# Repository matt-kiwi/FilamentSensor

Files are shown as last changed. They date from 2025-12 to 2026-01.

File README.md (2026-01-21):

# Filament sensor and controller

## Project summary / purpose

Used in the manufacturing process of making and recycling plastic. Specifically to detect if a strand of filament has been broken, then alert the operator with an audio alarm.

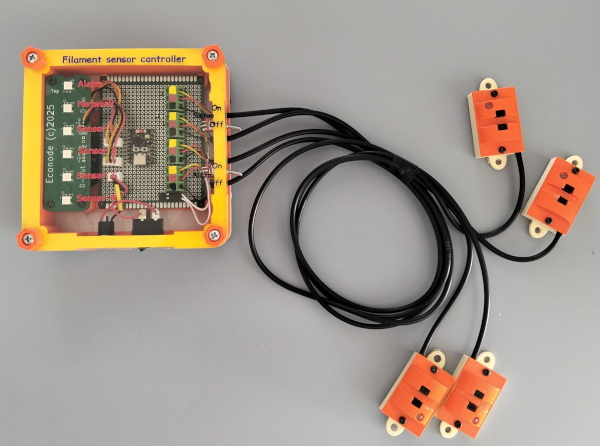
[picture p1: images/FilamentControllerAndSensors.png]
Filament Controller and Sensors


### Dedicated to Bill and Eva

This device is dedicated to Bill and Eva of KiwiFil plastics in New Zealand. And their pioneering work with plastics recycling.

## Usage and wiring

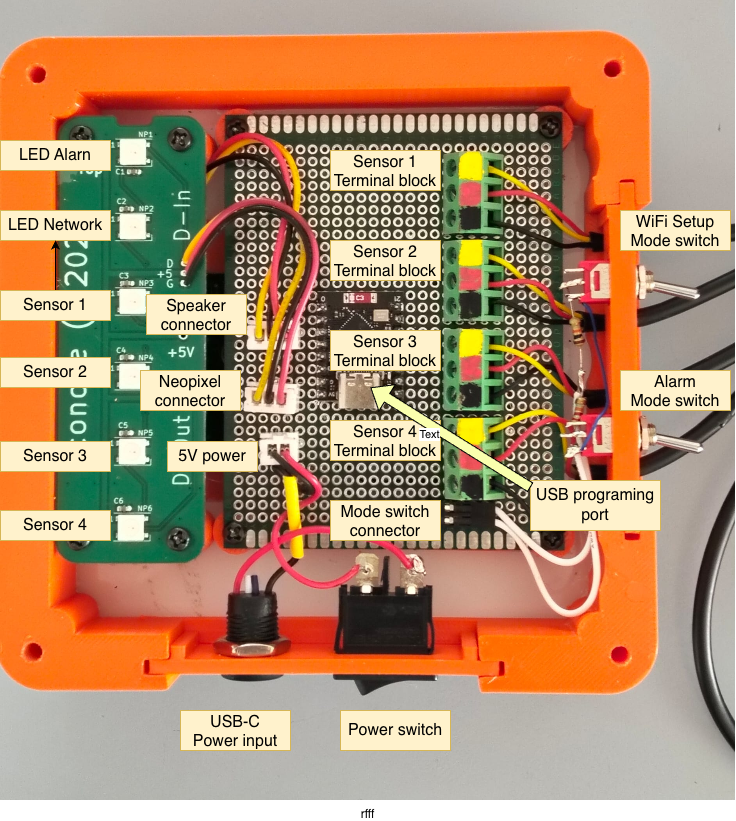
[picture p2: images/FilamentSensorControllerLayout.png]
Filamanet controller with labels


### Wiring

- Remove top lid with finger screws.
- Pull out switch block assembly / cable entry plate.
- Connect all 4 filament sensors using screw terminals, if a sensor is missing bridge Ground and Sensor input (Yellow).
- Install switch block assembly aligning sensor cables in combe/clamp.
- Install top lid

***Note that Siren / 12v Panel use lower 3pin JST for 12v in and Siren out Not shown in picture***

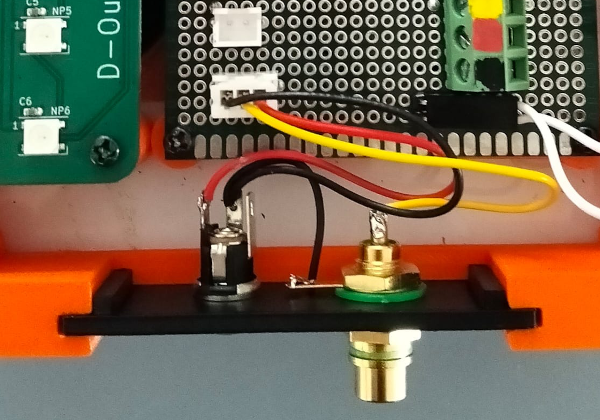
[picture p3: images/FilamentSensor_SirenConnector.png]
Siren panel


### Usage

Controller is powered by USB/5v some USB-C PD power supplies may not work.<br/>
Turn on power switch, during boot up the first LED will be blue, and a power up tune will be played.

\*\* One day when the WiFi software has been written the WiFi setup switch will enable configuring the WiFi

The "Alarm mode" switch enables or disables the audible alarm.

The alarm will sound when any of the sensors fail to detect filament.<br >
LEDs

- Alarm: Red in alarm, Green no alarm
- If a 12v Siren is connected it will sound.
- Sensors 1 - 4: Red in alarm, Green no alarm

Adjusting the volume, the underside of the controller has a 2 Watt speaker and volume control, turn clockwise to increase the volume.
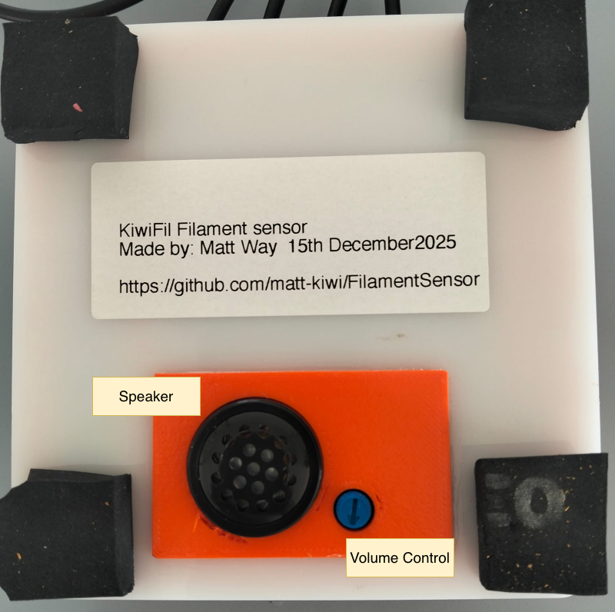
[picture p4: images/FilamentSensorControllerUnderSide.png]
Speaker and volume


## External Alarm / Siren

It was found the small 2w speaker was not loud enough for the factory background noise. So it was decided to attach a external 12volt Siren.

A 12v to 5v power module was added, and a small photo mosfet relay, so the ESP32 can switch on / off a small 12v load.
The optional siren is external and connected by a RCA/Coax connector.

### Siren 105dB

Siren from SurplusTronics  [Siren Piezo 105 dB 12 Volt DC](https://surplustronics.co.nz/products/4066-siren-piezo-105-db-12-volt-dc)

#### Two sirens with RCA plugs

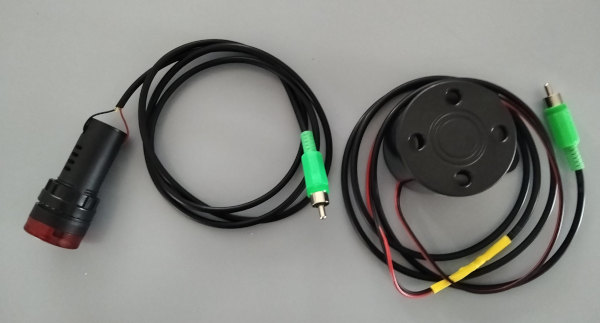
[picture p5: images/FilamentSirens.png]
Sirens on leads


#### 12V DC / Siren panel

Siren panel

## Serial Menu system

Some settings are user settable via the serial menu system, you will need to connect a USB-C cable to the internal USB-C port on the Super Mini, then use your favorite terminal program.

Mine is Cool Term by Roger Meiers [https://freeware.the-meiers.org/](https://freeware.the-meiers.org/)

Press enter twice to see menu options.

```TEXT
Reconnecting to /dev/cu.usbmodem1201 ...         Connected!
[I][MAIN] Initializing system...
[I][MAIN] =================================
[I][MAIN] Filament Sensor by Econode
[I][MAIN] =================================
[I][MAIN] Chip Model: ESP32-C3
[I][MAIN] Chip Revision: 4
[I][MAIN] CPU Frequency: 160 MHz
[I][MAIN] Flash Size: 4 MB
[I][MAIN] Free Heap: 261332 bytes
[I][MAIN] NeoPixel Pin: GPIO2
[I][MAIN] System initialized successfully!
[I][MAIN] =================================

                *############*.                                        
             +##################*-                                     
           .######################*:                                   
          .#########################+                                  
          *###########################=                                
          ##################################*                          
          -##############################% ##*.                        
           ###################################=                        
            +###################################+                      
              ########################+#####-=#####-                   
                .##################               ###=                 
                   ##*:=****=::                     .#*.               
                  ##=                                 .*=              
                 ##*                                    *+             
                ###*                                     :=            
              :#####*                                    =*=           
             *##########+                               -#*            
                                                       :#* 

         _  ___          _ ______ _ _     ___   ___ ___   __  
        | |/ (_)        (_)  ____(_) |   |__ \ / _ \__ \ / /  
        | ' / ___      ___| |__   _| |      ) | | | | ) / /_  
        |  < | \ \ /\ / / |  __| | | |     / /| | | |/ / '_ \ 
        | . \| |\ V  V /| | |    | | |    / /_| |_| / /| (_) |
        |_|\_\_| \_/\_/ |_|_|    |_|_|   |____|\___/____\___/ 

Available Tunes:
 0: JingleBells          1: Nokia                2: Mario                3: JamesBond         
 4: PinkPanther          5: ImperialMarch        6: AddamsFamily         7: MissionImpossible 
 8: IndianaJones         9: Tetris              10: HappyBirthday       11: Canon             
12: FurElise            13: GameOfThrones       14: HarryPotter         15: Zelda             
16: MarioPowerUp        17: StarWars            18: Beethoven5th        19: MontyPython       
20: MASH                21: Startup             22: Success             23: Error             
24: Alert               25: AmbientLoop       
Current alarm tune: 13 - GameOfThrones
Startup tune: 22 - Success

To select an alarm, type 'a' then the number (e.g. a15).
To select the startup tune, type 's' then the number (e.g. s21).
Type 'p' then number to play/test a song (e.g. p3), space to stop test.
Type 'c' to show current alarm and startup tune.
a19
Alarm tune selected: 19 - MontyPython

```

## Filament Sensor Optical

Using an IR slot sensor, commonly used for a speed / position sensor, can run at 3.3v or 5v.<br/>
Output is via LM393 voltage comparator producing a stable digital output with +VCC being open and 0V closed.

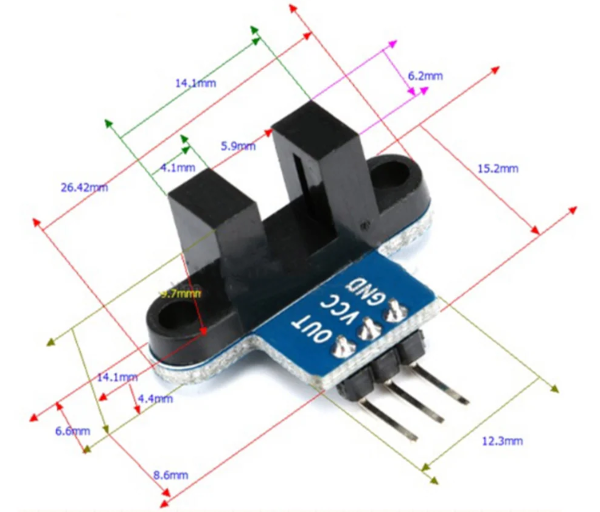
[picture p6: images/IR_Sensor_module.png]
Sensor module


STL files to print 3D printed casings can be found here [STL Files](hardware_optical_sensor)<br />
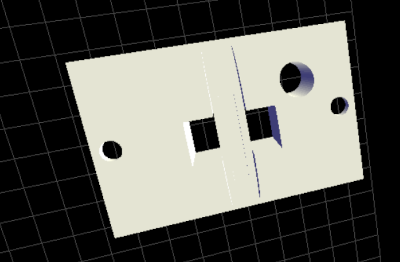
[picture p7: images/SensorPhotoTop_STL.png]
STL image sensor top
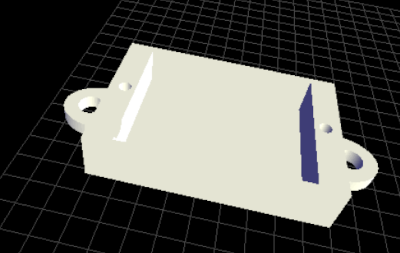
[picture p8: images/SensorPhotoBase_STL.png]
STL image sensor base
 <br />

Completed sensors with 3D printed housing<br />
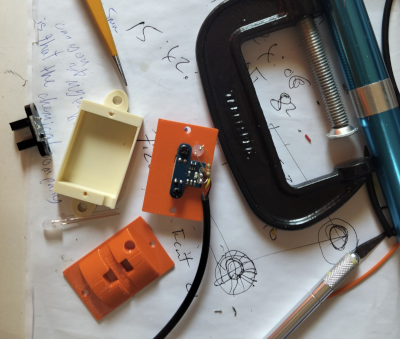
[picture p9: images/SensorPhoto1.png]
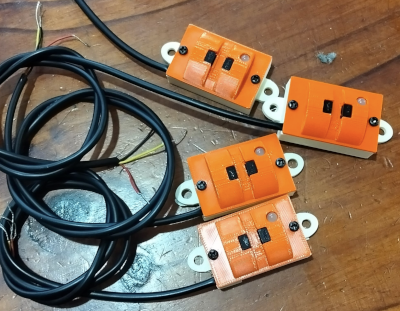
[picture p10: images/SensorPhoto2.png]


## Flament Sensor See Saw

The optical sensor had issues with translucent filaments, so a new mechanical design based on a kids see saw.
There is an M10 x 5 Magnet on the underside of the see saw, which biases the weight, and is used to close a reed switch. In the base there is a reed switch.

Closed IE pulled to ground is the Alarm condition, this is the reverse logic to the optical sensor.

### Assembly of sensor

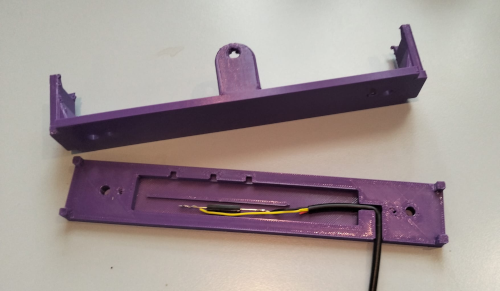
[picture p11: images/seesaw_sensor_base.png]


Install reed switch cable, adjust reed switch postion with trial assemble and set sensitivity / trigger point.

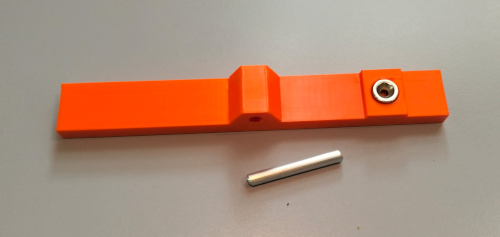
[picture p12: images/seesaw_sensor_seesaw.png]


Glue 10mm x 5mm disk magnet into underside of seesaw, and install piviot / axle.

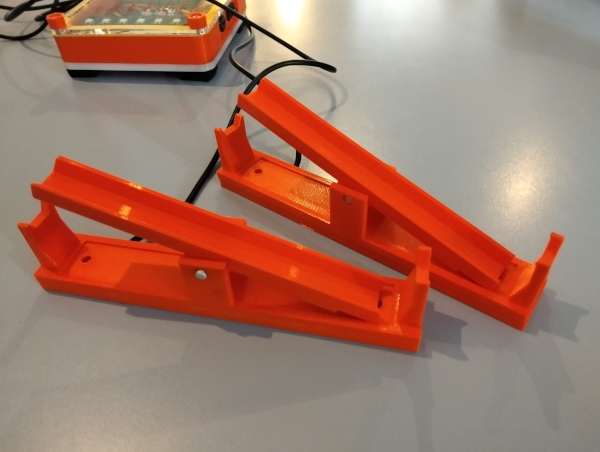
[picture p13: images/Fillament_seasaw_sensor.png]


#### STL files are here

- [sensor_seesaw_base_top.stl](hardware_seesaw_sensor/sensor_seesaw_base_top.stl)
- [sensor_seesaw_base_underside.stl](hardware_seesaw_sensor/sensor_seesaw_base_underside.stl)
- [sensor_seesaw_seesaw.stl](hardware_seesaw_sensor/sensor_seesaw_seesaw.stl)

## Controller

Hardware files, 3D print STL files, and laser cut SVGs can be found here [STL Files](hardware_ESP32_controller)

ESP32 C3 Super Mini

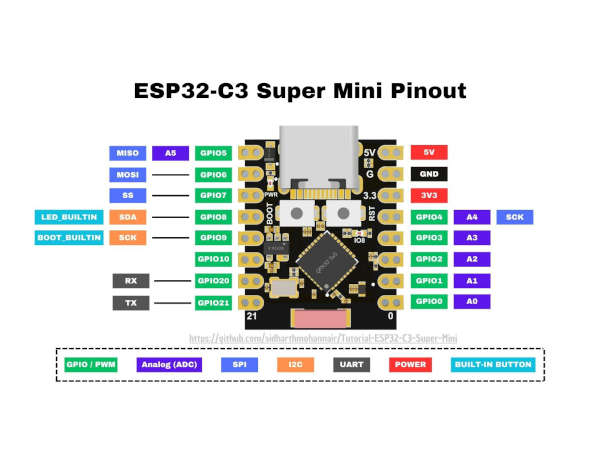
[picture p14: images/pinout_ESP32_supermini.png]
ESP32 Super mini pinout


CONNECTIONS:

- 5V → Power Input (USB or external 5V)
- GND → Common Ground
- 3V3 → 3.3V Output (for sensors)
- GPIO4 → Mode Switches (ADC input)
- GPIO3 → Speaker Output
- GPIO2 → NeoPixel Data
- GPIO5 → Sensor 4 Signal
- GPIO07 → Alarm / Relay
- GPIO10 → Sensor 3 Signal
- GPIO20 → Sensor 1 Signal
- GPIO21 → Sensor 2 Signal
- GPIO8 → Status LED (built-in)

## Schematic ( Vero Board prototype )

Schematic PDF File here: [FilamentSensorProjectVeroBoard.pdf](docs/FilamentSensorProjectVeroBoard.pdf)<br />
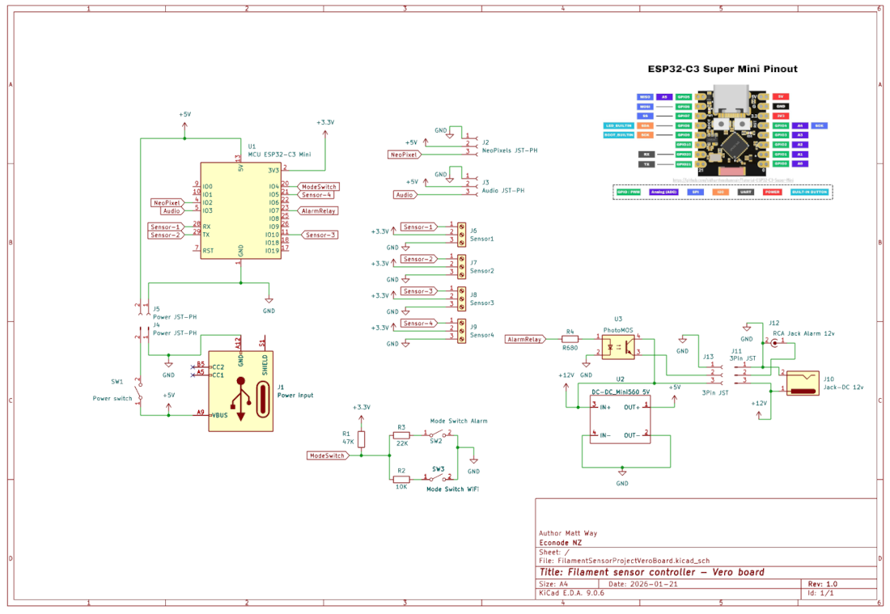
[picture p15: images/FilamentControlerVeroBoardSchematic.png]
Board Schematic


## Sound / Alarm

Alarm will sound when any of the 4 sensors don't detect any filament.<br />
Sound can be disabled by turning the "Alarm" switch to off.<br />
Volume can be adjusted by the volume knob on the underside of the control unit.<br />

The sound library is by Econode using RTTTL / Nokia ringtones.
[https://github.com/matt-kiwi/ESP32-C3-RTTTL_MusicPlayer](https://github.com/matt-kiwi/ESP32-C3-RTTTL_MusicPlayer)<br />

Amplifier and Speaker unit;<br />
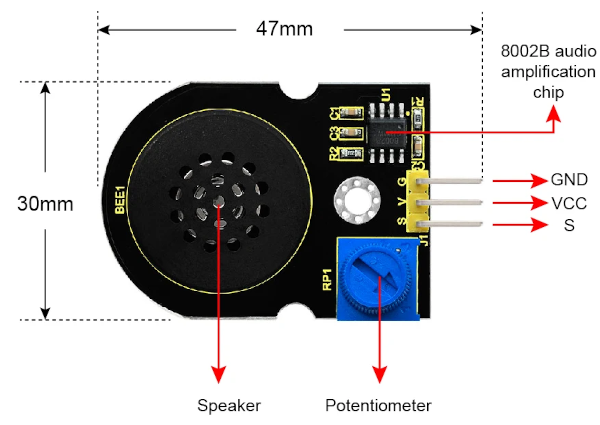
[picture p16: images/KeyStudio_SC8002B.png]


## Network / WiFi

Not currently implemented, the ESP32-C3 module has WiFi and antenna, there is a "setup mode" switch.

I envisage in the future all the factory alarms etc will be network enabled.

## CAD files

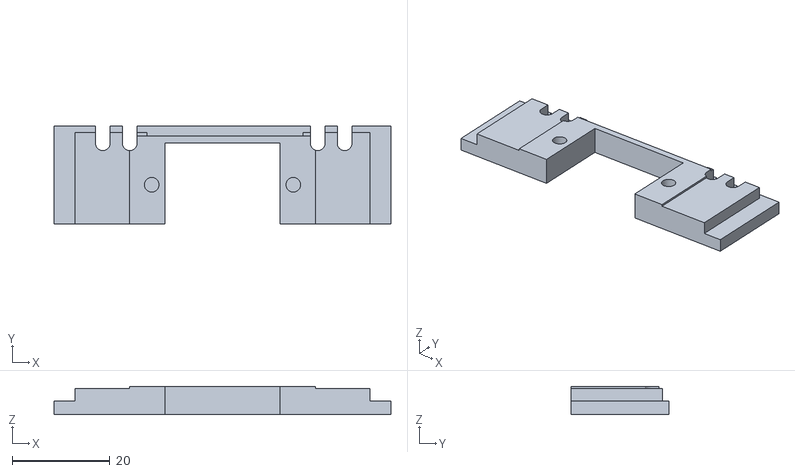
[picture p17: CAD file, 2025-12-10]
hardware_ESP32_controller/Filament_Controller_Piezo_Holder.stl
69.0 x 20.0 x 5.80

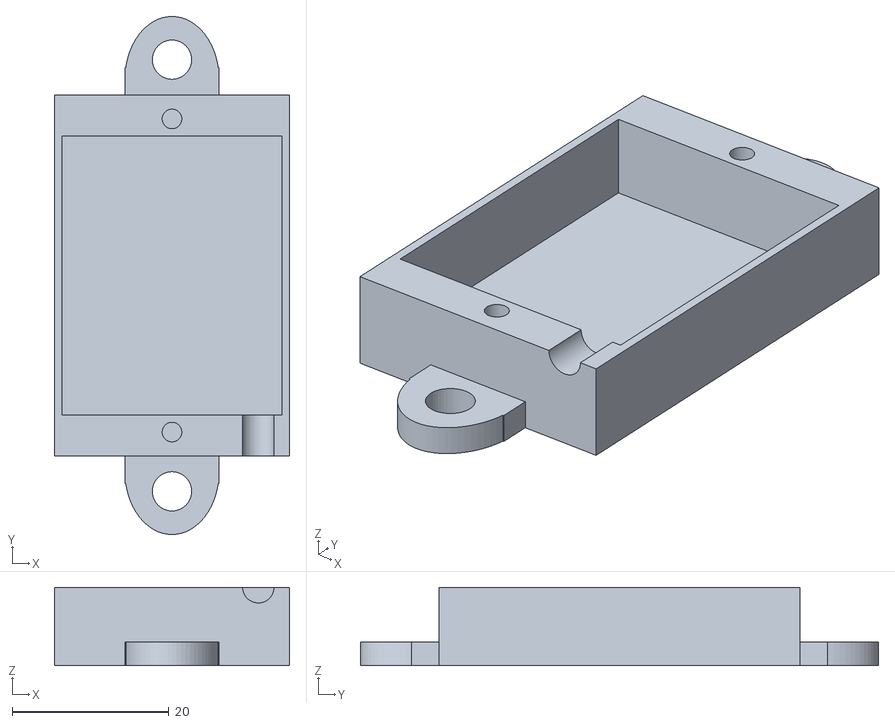
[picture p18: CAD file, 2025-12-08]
hardware_optical_sensor/Filament_senosr_base_v1.stl
30.0 x 66.0 x 10.0

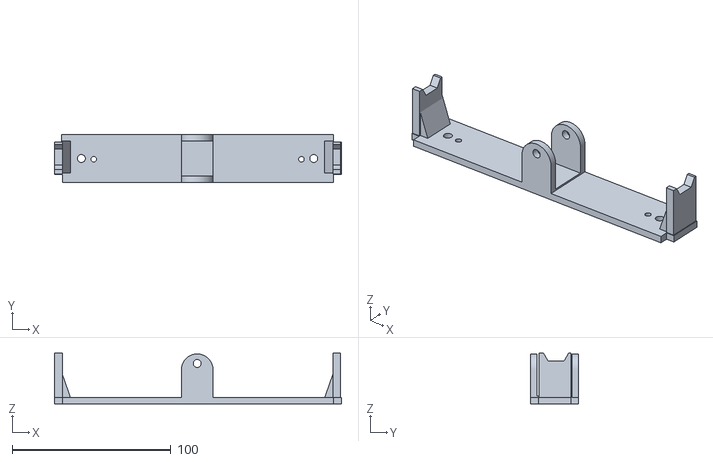
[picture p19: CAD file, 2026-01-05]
hardware_seesaw_sensor/sensor_seesaw_base_top.stl
181.0 x 30.0 x 32.0

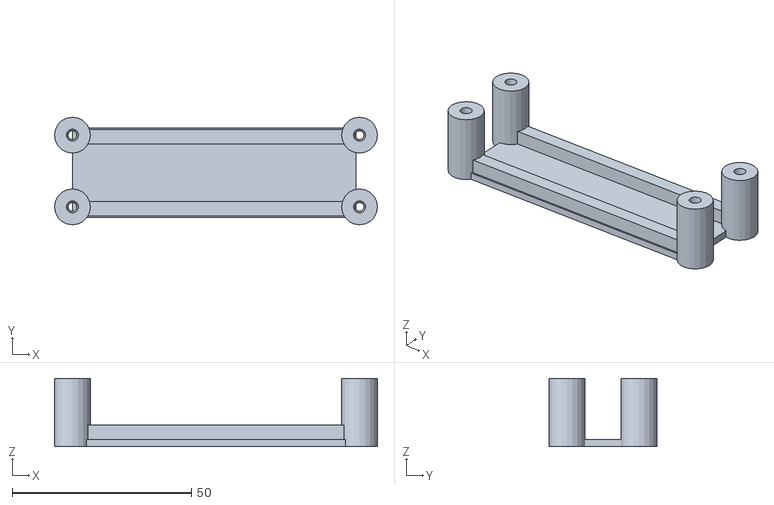
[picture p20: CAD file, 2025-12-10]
hardware_ESP32_controller/Filament_Controller_NeoPixel_Mount.stl
90.0 x 30.0 x 19.0

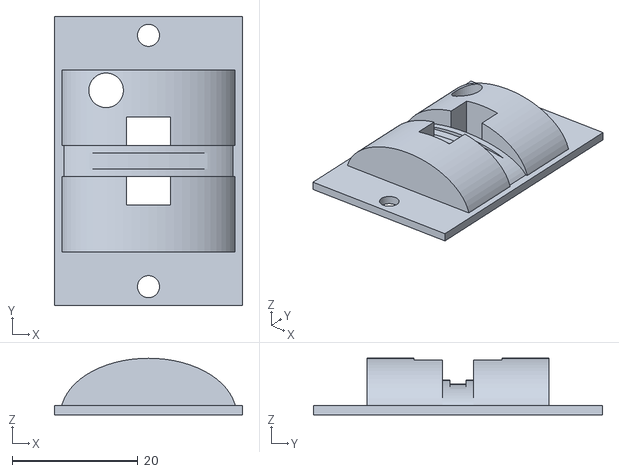
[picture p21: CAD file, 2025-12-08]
hardware_optical_sensor/Filament_sensor_top_v1.stl
30.0 x 46.0 x 9.00

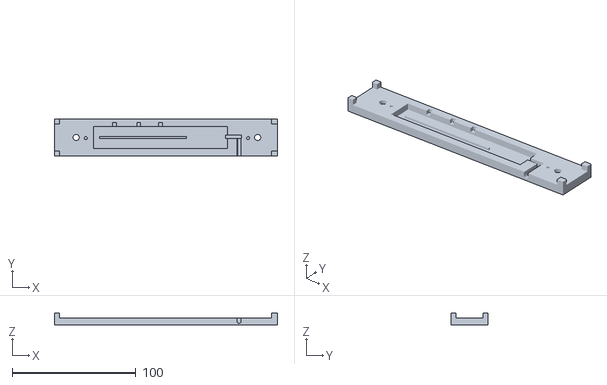
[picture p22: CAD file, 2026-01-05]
hardware_seesaw_sensor/sensor_seesaw_base_underside.stl
180.0 x 30.0 x 10.0

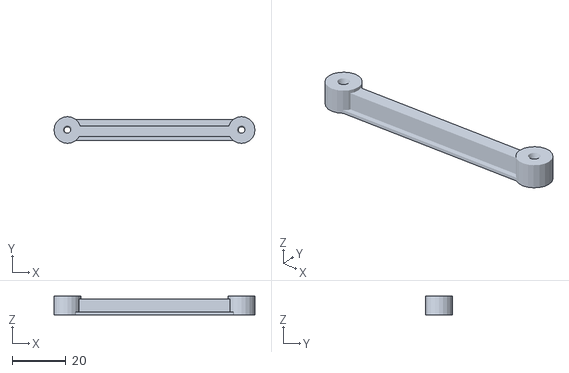
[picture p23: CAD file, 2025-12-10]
hardware_ESP32_controller/Filament_Controller_PCB_Mount.stl
75.0 x 10.0 x 7.00

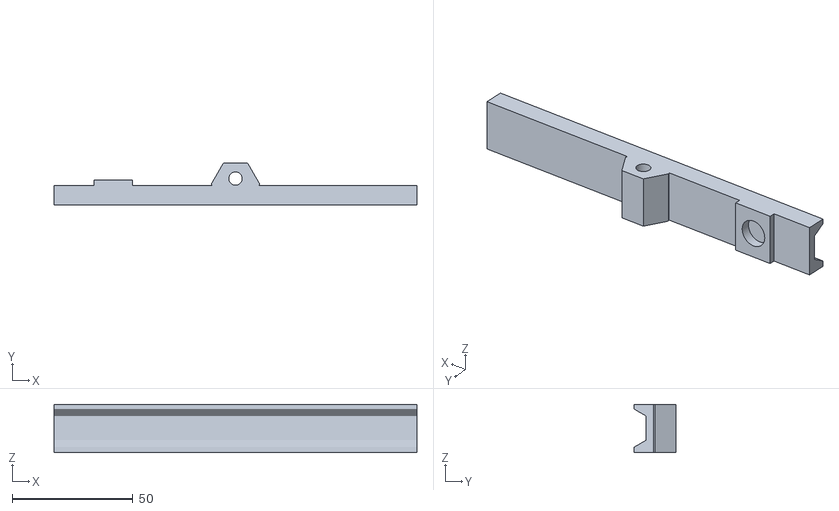
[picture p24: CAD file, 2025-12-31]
hardware_seesaw_sensor/sensor_seesaw_seesaw.stl
150.0 x 17.3 x 20.0

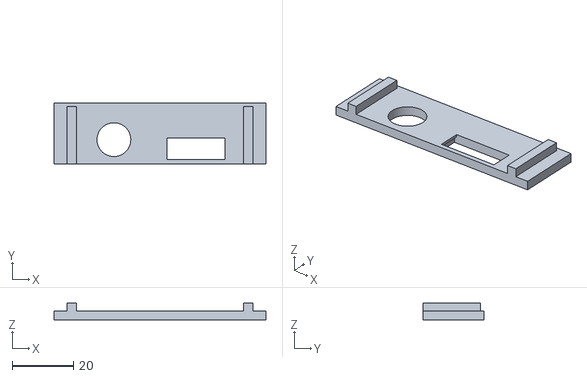
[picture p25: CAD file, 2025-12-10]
hardware_ESP32_controller/Filament_Controller_USB_Switch_Mount.stl
69.0 x 20.0 x 5.40

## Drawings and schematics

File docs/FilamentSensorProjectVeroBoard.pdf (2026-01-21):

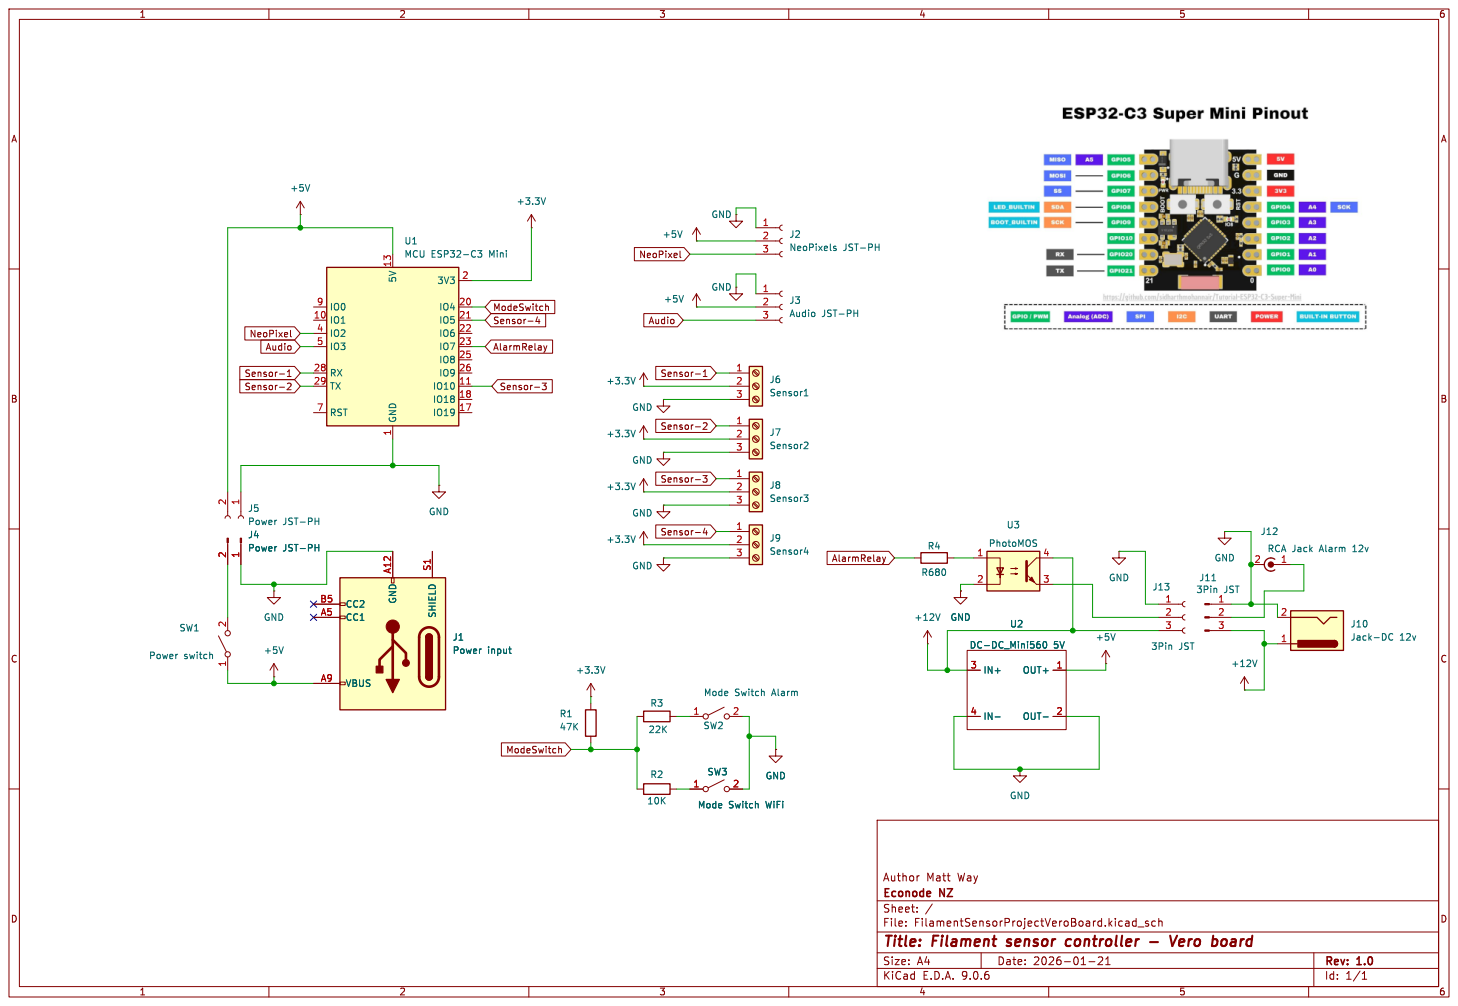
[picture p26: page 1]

J3Audio JST-PH GND GND

Id: 1/1 Title: Filament sensor controller - Vero board

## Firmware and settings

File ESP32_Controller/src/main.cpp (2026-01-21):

#include <Arduino.h>
#include <WiFi.h>
#include "LittleFS.h"
#include "stdint.h"
#define ECONODE_FILE_LOG_LEVEL 4
#include <Adafruit_NeoPixel.h>
#include "econode_logging.h"
// Set per-file log level to DEBUG
#define ECONODE_FILE_LOG_LEVEL 4


#include <RTTTL.h>

// RTTTL player object
RTTTL rtttl(PIN_AUDIO_OUT);




// Custom includes
#include "config.h"
#include "utils.h"
#include "globals.h"
#include "RTTTLTunes.h"
#include "serial_menu.h"

// Forward declarations
void loop100ms();
void loop1second();
void loop1minute();
void loop15minute();
void loop60minute();
void updateSensors();
void readModeSwitch();

// Initialize the Neopixel strip with Adafruit NeoPixel
Adafruit_NeoPixel strip(NUM_NEOPIXELS, NEOPIXEL_PIN, NEO_GRB + NEO_KHZ800);
global_t global;


// Helper functions for NeoPixels
void setPixelColor(uint8_t pixel, uint8_t r, uint8_t g, uint8_t b) {
    strip.setPixelColor(pixel, strip.Color(r, g, b));
}

void setPixelColor(uint8_t pixel, uint32_t color) {
    strip.setPixelColor(pixel, color);
}

void setAllPixels(uint8_t r, uint8_t g, uint8_t b) {
    uint32_t color = strip.Color(r, g, b);
    for(uint8_t i = 0; i < NUM_NEOPIXELS; i++) {
        strip.setPixelColor(i, color);
    }
}

void clearPixels() {
    strip.clear();
}

#include "splash_screen.h"

void setup() {
    pinMode(PIN_ALARM_RELAY, OUTPUT);
    digitalWrite(PIN_ALARM_RELAY, LOW);
    Serial.begin(115200);
    delay(2000);
    // Print welcome message and system info first
    LOG_I("MAIN", "Initializing system...");
    LOG_I("MAIN", "=================================");
    LOG_I("MAIN", "Filament Sensor by Econode");
    LOG_I("MAIN", "=================================");
    LOG_I("MAIN", "Chip Model: %s", ESP.getChipModel());
    LOG_I("MAIN", "Chip Revision: %d", ESP.getChipRevision());
    LOG_I("MAIN", "CPU Frequency: %d MHz", ESP.getCpuFreqMHz());
    LOG_I("MAIN", "Flash Size: %d MB", ESP.getFlashChipSize() / (1024 * 1024));
    LOG_I("MAIN", "Free Heap: %d bytes", ESP.getFreeHeap());
    LOG_I("MAIN", "NeoPixel Pin: GPIO%d", NEOPIXEL_PIN);
    LOG_I("MAIN", "System initialized successfully!");
    LOG_I("MAIN", "=================================");
    // Load alarm and startup tune from preferences
    menu_load_alarm_tune();
    // Now show splash screen and menu
    Serial.println(FPSTR(textSplashScreen));
    menu_init();
    global.epoch.lastSecondEpoch = millis();
    delay(1000); // Wait for serial to be ready
    pinMode(PIN_MODE_SWITCH, INPUT_PULLUP);
    readModeSwitch();
    // Initialize NeoPixel strip
    strip.begin();
    strip.setBrightness(25);
    setPixelColor(NEOPIXEL_ALARM, COLOR_PRE_BOOT);
    strip.show();
    // Play startup tune using ESP32-RTTTL
    rtttl.loadSong(rtttlTunes[menu_get_startup_tune()].song);
    rtttl.play();
    // Initialize sensor pins
    // Seesaw sensors (1 & 2) require pull-up
    pinMode(PIN_SENSOR_1, INPUT_PULLUP); // Seesaw
    pinMode(PIN_SENSOR_2, INPUT_PULLUP); // Seesaw
    pinMode(PIN_SENSOR_3, INPUT_PULLUP); // Seesaw
    pinMode(PIN_SENSOR_4, INPUT_PULLUP); // Seesaw
}

void loop() {
        menu_update();
    unsigned long currentMillis = millis();
    // 100ms tasks
    static unsigned long last100ms = 0;
    if (currentMillis - last100ms >= 100) {
        last100ms = currentMillis;
        loop100ms();
    }

    // 1 second tasks
    static unsigned long last1second = 0;
    if (currentMillis - last1second >= 1000) {
        last1second = currentMillis;
        loop1second();
        global.epoch.lastSecondEpoch++;
        global.epoch.uptimeSeconds = global.epoch.lastSecondEpoch;
    }

    // 1 minute tasks
    static unsigned long last1minute = 0;
    if (currentMillis - last1minute >= 60000) {
        last1minute = currentMillis;
        loop1minute();
    }

    // 15 minute tasks
    static unsigned long last15minute = 0;
    if (currentMillis - last15minute >= 900000) {
        last15minute = currentMillis;
        loop15minute();
    }

    // 60 minute tasks
    static unsigned long last60minute = 0;
    if (currentMillis - last60minute >= 3600000) {
        last60minute = currentMillis;
        loop60minute();
    }

    // Advance RTTTL playback
    rtttl.play();
}

void loop100ms() {
    // No player.loop() needed for spicajames/Rtttl

}

void loop1second() {
    readModeSwitch();
    // No player.stop() needed for spicajames/Rtttl
    if( global.modeSwitch.hasChanged ) global.modeSwitch.hasChanged = 0;
    updateSensors();

    // Update sensor LEDs
    setPixelColor(NEOPIXEL_ALARM, global.sensors.alarm?COLOR_SENSOR_FAIL:COLOR_SENSOR_OK);
    setPixelColor(NEOPIXEL_SENSOR1, global.sensors.s1_state?COLOR_SENSOR_FAIL:COLOR_SENSOR_OK);
    setPixelColor(NEOPIXEL_SENSOR2, global.sensors.s2_state?COLOR_SENSOR_FAIL:COLOR_SENSOR_OK);
    setPixelColor(NEOPIXEL_SENSOR3, global.sensors.s3_state?COLOR_SENSOR_FAIL:COLOR_SENSOR_OK);
    setPixelColor(NEOPIXEL_SENSOR4, global.sensors.s4_state?COLOR_SENSOR_FAIL:COLOR_SENSOR_OK);
    
    static bool alarmWasActive = false;
    int alarmTuneIndex = menu_get_selected_tune();
    if (global.sensors.hasChanged) {
        if (global.sensors.alarm) {
            if (global.modeSwitch.alarm) {
                // Only (re)start tune if not already playing
                if (!rtttl.isPlaying() || !alarmWasActive) {
                    rtttl.loadSong(rtttlTunes[alarmTuneIndex].song);
                    rtttl.play();
                }
                alarmWasActive = true;
            }
        } else {
            // Alarm condition cleared, stop playback
            if (alarmWasActive) {
                rtttl.stop();
            }
            alarmWasActive = false;
        }
        global.sensors.hasChanged = false;
    }
    // If alarm is still active and tune finished, restart it for continuous play
    if (global.sensors.alarm && global.modeSwitch.alarm && !rtttl.isPlaying()) {
        rtttl.loadSong(rtttlTunes[alarmTuneIndex].song);
        rtttl.play();
    }
    // Update NeoPixels
    strip.show();
    yield();

    // Control alarm relay
    if (global.sensors.alarm && global.modeSwitch.alarm) {
        digitalWrite(PIN_ALARM_RELAY, HIGH);
    } else {
        digitalWrite(PIN_ALARM_RELAY, LOW);
    }
}

void loop1minute() {
    // 1 minute log removed as requested
}

void loop15minute() {
    LOG_I("MAIN", "[15 Min] Periodic system check");
}

void loop60minute() {
    LOG_I("MAIN", "[Hour] Hourly maintenance");
}

void updateSensors(){
    // Seesaw sensors (1 & 2) are logic reversed
    int raw1 = digitalRead(PIN_SENSOR_1);
    int raw2 = digitalRead(PIN_SENSOR_2);
    int raw3 = digitalRead(PIN_SENSOR_3);
    int raw4 = digitalRead(PIN_SENSOR_4);
    uint8_t s1_state = !raw1; // Seesaw: invert logic
    uint8_t s2_state = !raw2; // Seesaw: invert logic
    uint8_t s3_state = !raw3; //  Seesaw: invert logic
    uint8_t s4_state = !raw4; // Seesaw: invert logic
    // LOG_D("SENSOR", "S1:%d (raw:%d) S2:%d (raw:%d) S3:%d (raw:%d) S4:%d (raw:%d)", s1_state, raw1, s2_state, raw2, s3_state, raw3, s4_state, raw4);
    uint8_t hasChanged = 0;
    uint8_t alarm,all_off;
    
    if( global.sensors.s1_state != s1_state ||  global.sensors.s2_state != s2_state || 
        global.sensors.s3_state != s3_state ||  global.sensors.s4_state != s4_state) hasChanged = 1;
    global.sensors.hasChanged = hasChanged;
    if( hasChanged ){
        global.sensors.s1_state = s1_state;
        global.sensors.s2_state = s2_state;
        global.sensors.s3_state = s3_state;
        global.sensors.s4_state = s4_state;
    }
    all_off = s1_state == 0 &&  s2_state == 0 && s3_state == 0 && s4_state == 0;
    global.sensors.all_off = all_off;
    alarm = !all_off;
    global.sensors.alarm = alarm;
}

void readModeSwitch(){
/*

 Two switches on a resistor ladder as follows

3.3V ─── 47kΩ ─── GPIO4 ──┬── 22kΩ ── SWITCH A ── GND
                          │
                         10kΩ
                          │
                          + ── SWITCH B ── GND
None: 4095
Switch A (22kΩ): 1434
Switch B (10kΩ): 780
Both: 570
*/
    uint16_t modeSwitchRaw = analogRead(PIN_MODE_SWITCH);
    bool modeSwitchSetup = false, modeSwitchAlarm = false;
    // Switch 1 logic - Alarm switch
    if( (modeSwitchRaw>1200 && modeSwitchRaw<1600) || (modeSwitchRaw>500 && modeSwitchRaw<600) ) modeSwitchAlarm = true;
    // Switch 2 logic - Setup switch
    if( (modeSwitchRaw>720 && modeSwitchRaw<820) || (modeSwitchRaw>500 && modeSwitchRaw<600) ) modeSwitchSetup = true;
    global.modeSwitch.hasChanged = global.modeSwitch.alarm != modeSwitchAlarm || global.modeSwitch.setup != modeSwitchSetup;
    global.modeSwitch.raw = modeSwitchRaw;
    global.modeSwitch.alarm = modeSwitchAlarm;
    global.modeSwitch.setup = modeSwitchSetup;
}

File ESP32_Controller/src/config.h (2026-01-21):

#pragma once

#define PIN_SENSOR_1     20
#define PIN_SENSOR_2     21
#define PIN_SENSOR_3     10
#define PIN_SENSOR_4     5

#define PIN_ALARM_RELAY   7

// Alarm threshold in milliseonds, IE delay to start alarm
#define ALARM_THRESHOLD  3000

// NeoPixel LED Strip (6 LEDs for status indication)
#define NEOPIXEL_PIN      2
#define NUM_NEOPIXELS     6

// Colors
#define COLOR_SENSOR_OK   strip.Color(0, 255, 0)   // Green
#define COLOR_SENSOR_FAIL strip.Color(255, 0, 0)   // Red
#define COLOR_PRE_BOOT    strip.Color(0, 0, 255)   // Blue
#define COLOR_BOOT_OK     strip.Color(0, 255, 0)   // Green

#define NEOPIXEL_ALARM    0
#define NEOPIXEL_NETWORK  1
#define NEOPIXEL_SENSOR1  2
#define NEOPIXEL_SENSOR2  3
#define NEOPIXEL_SENSOR3  4
#define NEOPIXEL_SENSOR4  5

// Audio out / RTTTL pin
#define PIN_AUDIO_OUT        3

/*
Setup and Alarm switches (Resistor Ladder to Single ADC)

3.3V ─── 47kΩ ─── GPIO4 ──┬── 22kΩ ── SWITCH A ── GND
                          │
                         10kΩ
                          │
                          + ── SWITCH B ── GND
*/
#define PIN_MODE_SWITCH  4  // GPIO4 - ADC1_CH3 (0-3.3V analog input)

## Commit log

2025-12-08 Update readme, ESP32 pin assignments
2025-12-08 read me update
    [Filament_senosr_base_v1.stl, Filament_sensor_top_v1.stl]
2025-12-10 Add laser cut SVG files
2025-12-10 Added 3D print STL files for the ESP32 controller casing
    [Filament_Controller_NeoPixel_Mount.stl, Filament_Controller_PCB_Mount.stl, Filament_Controller_Piezo_Holder.stl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]
2025-12-10 Setup Neopixels, added tests for the sensors, making progress
2025-12-15 Added SVG laser cuts
2025-12-16 Updated SVG cut files
2025-12-17 Added Ki-Cad project files
    [FilamentSensorProjectVeroBoard.kicad_pcb, FilamentSensorProjectVeroBoard.kicad_sch]
2025-12-17 Added Vero Board Shematic
    [FilamentSensorProjectVeroBoard.kicad_sch]
2025-12-31 Added logging, and change sensors 1&2 to SeeSaw
2025-12-31 Updated docs, Seesaw sensor + images
    [sensor_seesaw_base_top.stl, sensor_seesaw_base_underside.stl, sensor_seesaw_seesaw.stl]
2026-01-05 Changed all 4 sensors to Seesaw
2026-01-05 Updates readme.
    New STl files and instructions for the seesaw sensor
    [sensor_seesaw_base_top.stl, sensor_seesaw_base_underside.stl]
2026-01-21 Added external siren code, updated schematic
    [FilamentSensorProjectVeroBoard.kicad_sch]
2026-01-21 Updated Readme for 12v / Siren conversion
